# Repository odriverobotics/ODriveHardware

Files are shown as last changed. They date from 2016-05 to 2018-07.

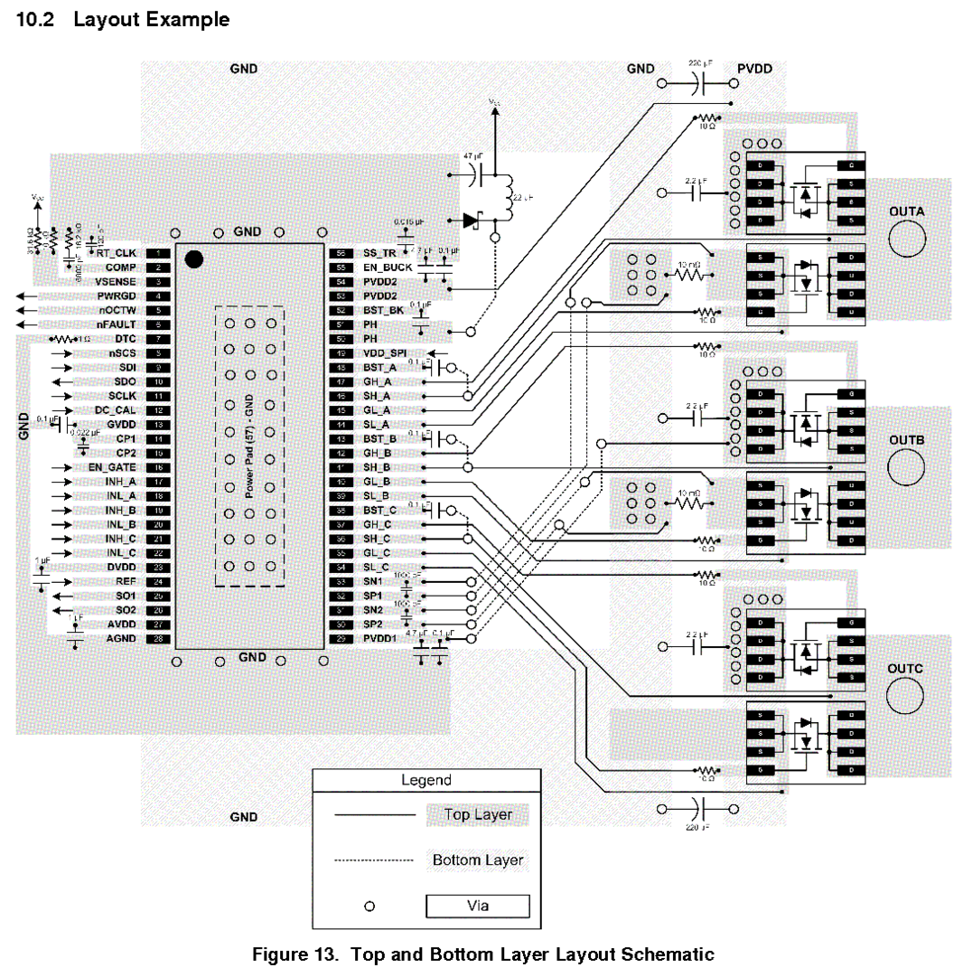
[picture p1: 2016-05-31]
v3/layoutexample.PNG

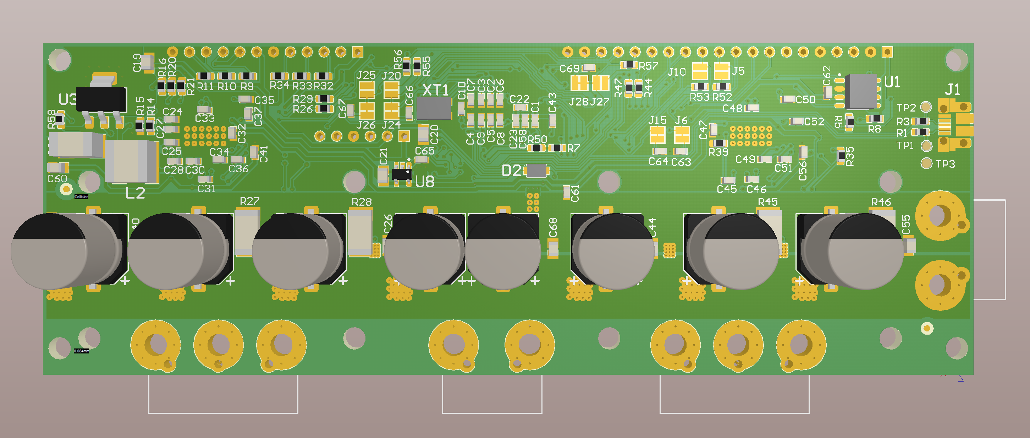
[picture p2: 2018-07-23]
v3/v3.5docs/v3.5_bottom.PNG

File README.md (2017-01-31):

# ODriveHardware
This project is all about accuratly driving brushless motors, for cheap. The aim is to make it possible to use inexpensive brushless motors in high performance robotics projects.
Like this (click for video):
Servo motor control demo (https://www.youtube.com/watch?v=WT4E5nb3KtY)

If you want to get your hands on a board, check out [this post](https://hackaday.io/project/11583-odrive-high-performance-motor-control/log/40702-boards-and-development).

This repository contains the circuit board design of ODrive. The other related repositories are:
* [ODriveFirmware](https://github.com/madcowswe/ODriveFirmware): Firmware that runs on the board.
* [ODrive](https://github.com/madcowswe/ODrive): Configuration and analysis scripts that runs on a PC.

There is also [ODriveFPGA](https://github.com/madcowswe/ODriveFPGA), which contains the FPGA logic and software that runs on the FPGA based ODrive. This is not currently in development, but may be resumed at some later date.

## Odrive v3 board
The pinout from the microcontroller to the board is documented [here](https://docs.google.com/spreadsheets/d/1QXDCs1IRtUyG__M_9WruWOheywb-GhOwFtfPcHuN2Fg/edit?usp=sharing).

### Pictures!
Odrive v3.1 top
Odrive v3.1 bottom

### ODrive v3.1 errata
* The silkscreen labels for the encoders (M0, M1) are reversed.
* The output impedence of the current amplifiers were not considered when designing the post-amplifier filters. Hence the response is about 5x slower than designed. Max allowed modulation index is therefore about 50%.

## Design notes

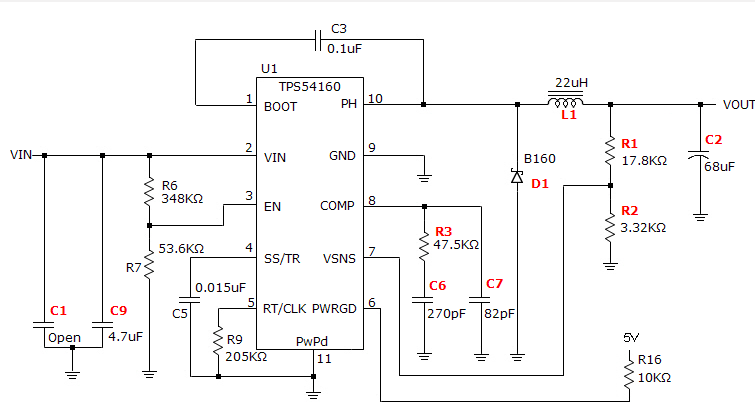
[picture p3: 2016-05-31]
v3/swticher pro design.PNG

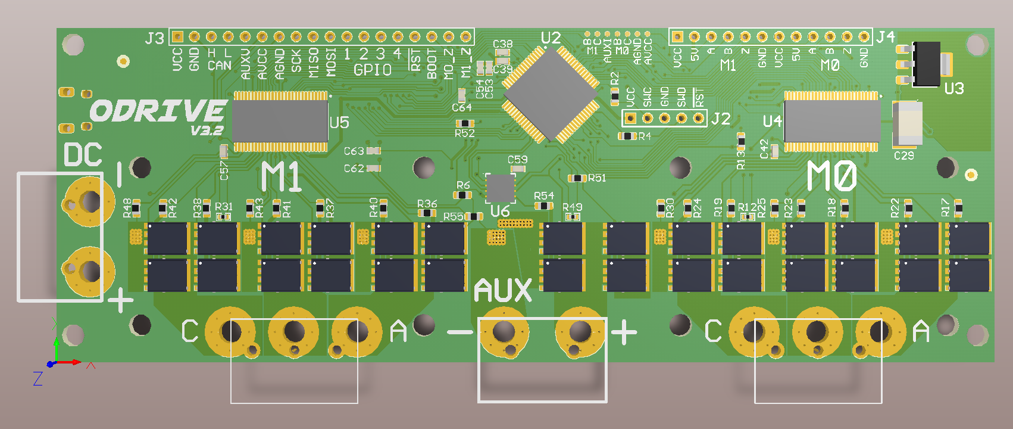
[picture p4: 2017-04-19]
v3/v3.2docs/v3.2_top.PNG

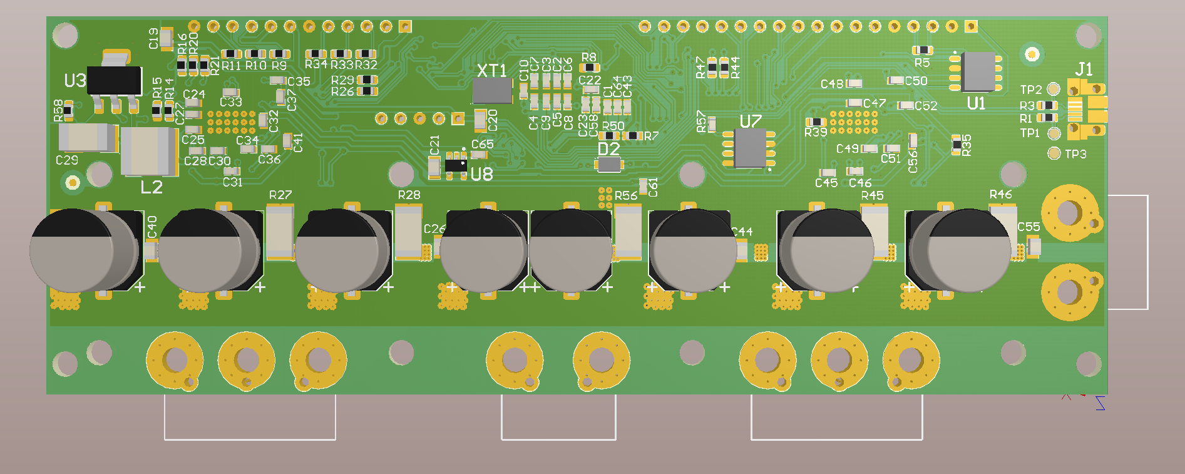
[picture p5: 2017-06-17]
v3/v3.3docs/v3.3_bottom.PNG

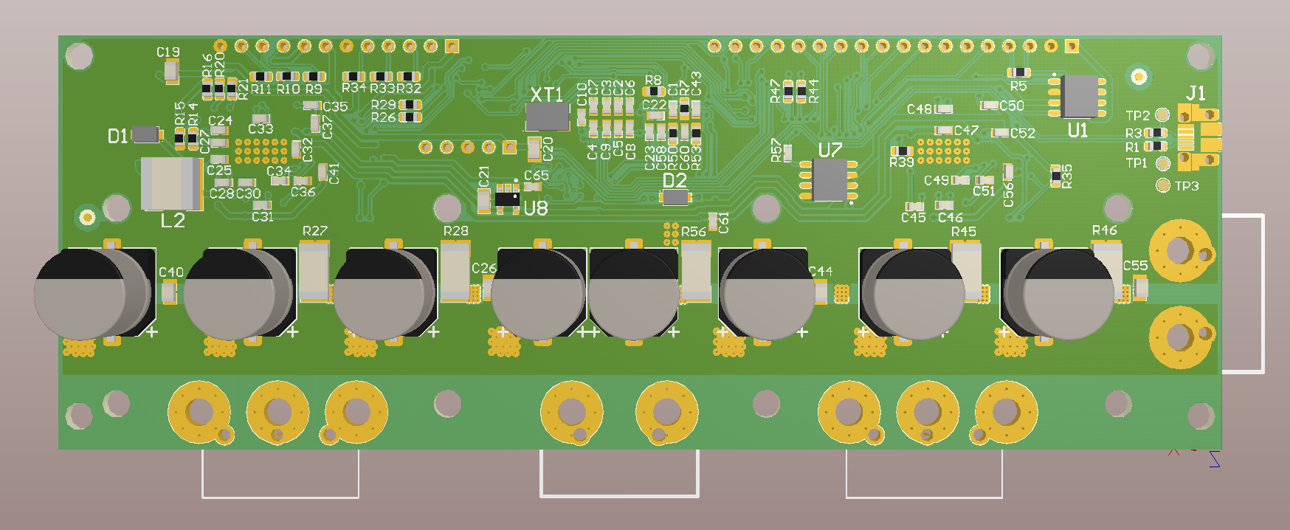
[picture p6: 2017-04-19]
v3/v3.2docs/v3.2_bottom.PNG

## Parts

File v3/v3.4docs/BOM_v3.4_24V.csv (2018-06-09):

Quantity | Designator | Description | Voltage - Rated | Comment | LibRef
14 | C1, C4, C5, C23, C32, C35, C37, C43, C47, C50, C52, C58, C61, C65 | CAP CER 2.2UF 16V X5R 0603 | 16V | 2.2µF | GRM188R61C225KE15D
2 | C2, C3 | CAP CER 10PF 50V NP0 0603 | 50V | 10pF | GRM1885C1H100JA01D
18 | C6, C7, C8, C9, C10, C22, C25, C28, C30, C31, C34, C41, C45, C46, C49, C56, C59, C63 | CAP CER 0.1UF 50V X7R 0603 | 50V | 0.1uF | GRM188R71H104KA93D
8 | C11, C12, C13, C14, C15, C16, C17, C18 | CAP, FP Series, 470 µF, 25 V, Radial Can - SMD, 10 mm |  | 470uF | EEEFP1E471AP
8 | C19, C20, C21, C26, C40, C44, C55, C60 | CAP CER 4.7UF 35V X5R 0805 | 35V | 4.7uF | GRM219R6YA475KA73D
1 | C24 | CAP CER 82PF 100V NP0 0603 | 100V | 82pF | GRM1885C2A820JA01D
1 | C27 | CAP CER 270PF 50V NP0 0603 | 50V | 270pF | GRM1885C1H271JA01D
1 | C29 | CAP TANT 68UF 16V 20% 2312 250mOhm |  | 68uF | T495C686M016ATE250
2 | C33, C48 | CAP CER 0.022UF 50V X7R 0603 | 50V | 0.022µF | GRM188R71H223KA01D
10 | C36, C38, C39, C42, C51, C53, C54, C57, C62, C64 | CAP CER 2200PF 50V NP0 0603 | 50V | 2200pF | GRM1885C1H222JA01D
2 | D1, D2 | Rectifier Diode, Single, 40 V, 1 A, SOD-123FL, 2, 550 mV |  |  | MBR140SFT1G
4 | FID1, FID2, FID3, FID4 | 1mm Fiducial with 2mm soldermask, 3mm keepout |  | FIDUCIAL | FIDUCIAL
12 | H1, H2, H3, H4, H5, H6, H7, H8, H9, H10, H11, H12 | M3 Hole with no copper |  |  | M3 Hole
1 | J1 | MICRO USB B, RECEPTACLE, SMT, RA, 5WAY |  |  | 10103594-0001LF
1 | J2 | Header, 5-Pin |  |  | Header 5
1 | J3 | Header, 18-Pin |  | Leftheader | Header 18
1 | J4 | Header, 12-Pin |  | Rightheader | Header 12
10 | J7, J8, J11, J12, J13, J16, J17, J18, J21, J22 | M3 Spade Terminal |  |  | M3 Spade Terminal
2 | J9, J23 | CONN TERM BLOCK 2POS 7.62MM |  | 1868076 | 1868076
2 | J14, J19 | CONN TERM BLOCK 3POS 7.62MM |  | 1704936 | 1704936
1 | L2 | INDUCTOR 22UH 1.4A 175.5 MOHM |  | 22uH | NR6028T220M
1 | LED1 | LED GREEN CLEAR 0603 SMD |  | Green | LTST-C190KGKT
28 | Q1, Q2, Q3, Q4, Q5, Q6, Q7, Q8, Q9, Q10, Q11, Q12, Q13, Q14, Q15, Q16, Q17, Q18, Q19, Q20, Q21, Q22, Q23, Q24, Q25, Q26, Q27, Q28 | MOSFET N-CH 30V 13A SO8FL |  | [NoValue], FILL_FOOTPRINT, [NoValue], FILL_FOOTPRINT, [NoValue], FILL_FOOTPRINT, [NoValue], [NoValue], [NoValue], [NoValue], [NoValue], [NoValue], [NoValue], FILL_FOOTPRINT, [NoValue], FILL_FOOTPRINT, [NoValue], FILL_FOOTPRINT, [NoValue], [NoValue], [NoValue], [NoValue], [NoValue], [NoValue], FILL_FOOTPRINT, [NoValue], [NoValue], [NoValue] | NTMFS4935NT1G
8 | R1, R2, R3, R4, R26, R29, R44, R47 | RES SMD 22 OHM 1% 1/10W 0603 |  | 22R | RC0603FR-0722RL
7 | R5, R25, R30, R43, R48, R55, R57 | RES SMD 120 OHM 1% 1/10W 0603 |  | 120R | RC0603FR-07120RL
1 | R6 | RES SMD 10K OHM 1% 1/10W 0603 |  | 10K | RC0603FR-0710KL
2 | R7, R58 | RES SMD 1K OHM 1% 1/10W 0603 |  | 1k | RC0603FR-071KL
2 | R8, R14 | RES SMD 47K OHM 1% 1/10W 0603 |  | 47K | RC0603FR-0747KL
10 | R9, R10, R11, R13, R20, R32, R33, R34, R35, R50 | RES SMD 3.3K OHM 1% 1/10W 0603 |  | 3.3k | RC0603FR-073K3L
3 | R12, R31, R49 | THERMISTOR 10K OHM NTC 0402 SMD |  | 10k | NCP15XH103F03RC
1 | R15 | RES SMD 220K OHM 1% 1/10W 0603 |  | 220k | RC0603FR-07220KL
3 | R16, R21, R39 | RES SMD 18K OHM 1% 1/10W 0603 |  | 18k | RC0603FR-0718KL
14 | R17, R18, R19, R22, R23, R24, R36, R37, R38, R40, R41, R42, R51, R54 | RES SMD 2.2 OHM 1% 1/10W 0603 |  | 2.2R | RC0603FR-072R2L
5 | R27, R28, R45, R46, R56 | RES SMD 0.0005 OHM 1% 3W 2512 |  | 500uOhm | CSR2512C0R0005F
1 | U1 |  |  | SN65HVD232D | SN65HVD232D
1 | U2 | ARM Cortex-M4 32-bit MCU+FPU, 210 DMIPS, 1024 kB Flash, 192 kB Internal RAM, 51 I/Os, 64-pin LQFP, -40 to 85 degC, Tray |  |  | STM32F405RGT6
1 | U3 | IC REG LDO 3.3V 1A SOT223 |  | 3.3V | AZ1117EH-3.3TRG1
2 | U4, U5 | MOTOR DRIVER, 3PH, 56HTSSOP |  |  | DRV8301
1 | U6 | DRIVER, MOSFET, HALF BRIDGE, WSON-8, 1A |  |  | LM5109BSD/NOPB
1 | U7 | ANALOG DEVICES Current Sense Amplifier, Bidirectional, 1, 130 µA, NSOIC |  |  | AD8418WBRZ
1 | U8 | IC REG LDO 3.3V 0.25A SOT23-5 |  | 3.3V | LP5907MFX-3.3/NOPB
1 | XT1 | Crystal 8MHz ±10ppm 10pF 200 Ohm -10°C ~ 60°C Surface Mount 4-SMD, No Lead (DFN, LCC) |  | 8 MHz | ABM3B-8.000MHZ-10-1-U-T

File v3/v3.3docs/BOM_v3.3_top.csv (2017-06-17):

Quantity | Designator | Description | Comment | LibRef | Layer
7 | C38, C39, C42, C53, C54, C57, C62 | CAP CER 2200PF 50V NP0 0603 | 2200pF | GRM1885C1H222JA01D | Top
2 | C59, C63 | CAP CER 0.1UF 25V X7R 0603 | 0.10µF | GRM188R71E104KA01D | Top
1 | D1 | Rectifier Diode, Single, 40 V, 1 A, SOD-123FL, 2, 550 mV |  | MBR140SFT1G | Top
2 | FID1, FID3 | 1mm Fiducial with 2mm soldermask, 3mm keepout | FIDUCIAL | FIDUCIAL | Top
12 | H1, H2, H3, H4, H5, H6, H7, H8, H9, H10, H11, H12 | M3 Hole with no copper |  | M3 Hole | Top
1 | J2 | Header, 5-Pin |  | Header 5 | Top
1 | J3 | Header, 18-Pin | Leftheader | Header 18 | Top
1 | J4 | Header, 12-Pin | Rightheader | Header 12 | Top
10 | J7, J8, J11, J12, J13, J16, J17, J18, J21, J22 | M3 Spade Terminal |  | M3 Spade Terminal | Top
2 | J9, J23 | CONN TERM BLOCK 2POS 7.62MM | 1868076 | 1868076 | Top
2 | J14, J19 | CONN TERM BLOCK 3POS 7.62MM | 1704936 | 1704936 | Top
1 | LED1 | LED GREEN CLEAR 0603 SMD | Green | LTST-C190KGKT | Top
28 | Q1, Q2, Q3, Q4, Q5, Q6, Q7, Q8, Q9, Q10, Q11, Q12, Q13, Q14, Q15, Q16, Q17, Q18, Q19, Q20, Q21, Q22, Q23, Q24, Q25, Q26, Q27, Q28 | MOSFET N-CH 30V 13A SO8FL |  | NTMFS4935NT1G | Top
2 | R2, R4 | RES SMD 22 OHM 1% 1/10W 0603 | 22R | RC0603FR-0722RL | Top
1 | R6 | RES SMD 10K OHM 1% 1/10W 0603 | 10K | RC0603FR-0710KL | Top
3 | R12, R31, R49 | THERMISTOR 10K OHM NTC 0402 SMD | 10k | NCP15XH103F03RC | Top
1 | R13 | RES SMD 3.3K OHM 1% 1/10W 0603 | 3.3k | RC0603FR-073K3L | Top
14 | R17, R18, R19, R22, R23, R24, R36, R37, R38, R40, R41, R42, R51, R54 | RES SMD 2.2 OHM 1% 1/10W 0603 | 2.2R | RC0603FR-072R2L | Top
5 | R25, R30, R43, R48, R55 | RES SMD 120 OHM 1% 1/10W 0603 | 120R | RC0603FR-07120RL | Top
1 | U2 | ARM Cortex-M4 32-bit MCU+FPU, 210 DMIPS, 1024 kB Flash, 192 kB Internal RAM, 51 I/Os, 64-pin LQFP, -40 to 85 degC, Tray |  | STM32F405RGT6 | Top
2 | U4, U5 | MOTOR DRIVER, 3PH, 56HTSSOP |  | DRV8301 | Top
1 | U6 | DRIVER, MOSFET, HALF BRIDGE, WSON-8, 1A |  | LM5109BSD/NOPB | Top

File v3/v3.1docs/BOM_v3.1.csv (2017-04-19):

Quantity | Designator | Description | Comment | LibRef
14 | C1, C4, C5, C23, C32, C35, C37, C43, C47, C50, C52, C58, C60, C61 | CAP CER 2.2UF 16V X5R 0603 | 2.2µF | GRM188R61C225KE15D
2 | C2, C3 | CAP CER 10PF 50V NP0 0603 | 10pF | GRM1885C1H100JA01D
18 | C6, C7, C8, C9, C10, C22, C25, C28, C30, C31, C34, C41, C45, C46, C49, C56, C59, C63 | CAP CER 0.1UF 25V X7R 0603 | 0.10µF | GRM188R71E104KA01D
8 | C11, C12, C13, C14, C15, C16, C17, C18 | CAP, FP Series, 470 µF, 25 V, Radial Can - SMD, 10 mm | 470uF | EEEFP1E471AP
7 | C19, C20, C21, C26, C40, C44, C55 | CAP CER 4.7UF 35V X5R 0805 | 4.7uF | GRM219R6YA475KA73D
1 | C24 | CAP CER 82PF 100V NP0 0603 | 82pF | GRM1885C2A820JA01D
1 | C27 | CAP CER 270PF 50V NP0 0603 | 270pF | GRM1885C1H271JA01D
1 | C29 | CAP TANT 68UF 16V 20% 2312 250mOhm | 68uF | T495C686M016ATE250
11 | C33, C36, C38, C39, C42, C48, C51, C53, C54, C57, C62 | CAP CER 0.022UF 25V X7R 0603 | 0.022µF | GRM188R71E223KA01D
2 | D1, D2 | Rectifier Diode, Single, 40 V, 1 A, SOD-123FL, 2, 550 mV |  | MBR140SFT1G
12 | H1, H2, H3, H4, H5, H6, H7, H8, H9, H10, H11, H12 | M3 Hole with no copper |  | M3 Hole
1 | J1 | MICRO USB B, RECEPTACLE, SMT, RA, 5WAY |  | 10103594-0001LF
3 | J2, J10, J15 | Header, 5-Pin |  | Header 5
1 | J3 | Header, 3-Pin |  | Header 3
1 | J4 | Header, 4-Pin |  | Header 4
1 | J5 | Header, 3-Pin, Dual row |  | Header 3X2
1 | J6 | Header, 8-Pin |  | Header 8
10 | J7, J8, J11, J12, J13, J16, J17, J18, J21, J22 | M3 Spade Terminal |  | M3 Spade Terminal
2 | J9, J23 | MULTICOMP Wire-To-Board Terminal Block, 2, 600 V, 30 A, 24 AWG, 10 AWG |  | MC000054
2 | J14, J19 | TERMINAL BLOCK, WIRE TO BRD, 3POS, 10AWG |  | MC000051
1 | J20 | Socket | AuxV | Socket
1 | L1 | FERRITE BEAD, 0.1OHM, 2A, 0805 | 600ohm | 2508056017Y2
1 | L2 | INDUCTOR 22UH 1.4A 175.5 MOHM | 22uH | NR6028T220M
28 | Q1, Q2, Q3, Q4, Q5, Q6, Q7, Q8, Q9, Q10, Q11, Q12, Q13, Q14, Q15, Q16, Q17, Q18, Q19, Q20, Q21, Q22, Q23, Q24, Q25, Q26, Q27, Q28 | MOSFET, N CH, 30V, 70A, SO-8 FL |  | NTMFS4937NT1G
13 | R1, R2, R3, R4, R25, R26, R29, R30, R43, R44, R47, R48, R55 | RES SMD 22 OHM 1% 1/10W 0603 | 22R | RC0603FR-0722RL
1 | R5 | RES SMD 120 OHM 1% 1/10W 0603 | 120R | RC0603FR-07120RL
2 | R6, R52 | RES SMD 10K OHM 1% 1/10W 0603 | 10K | RC0603FR-0710KL
8 | R7, R9, R10, R11, R32, R33, R34, R53 | RES SMD 1K OHM 1% 1/10W 0603 | 1k | RC0603FR-071KL
2 | R8, R14 | RES SMD 47K OHM 1% 1/10W 0603 | 47K | RC0603FR-0747KL
3 | R12, R31, R49 | THERMISTOR 10K OHM NTC 0402 SMD | 10k | NCP15XH103F03RC
4 | R13, R20, R35, R50 | RES SMD 3.3K OHM 1% 1/10W 0603 | 3.3k | RC0603FR-073K3L
1 | R15 | RES SMD 220K OHM 1% 1/10W 0603 | 220k | RC0603FR-07220KL
3 | R16, R21, R39 | RES SMD 18K OHM 1% 1/10W 0603 | 18k | RC0603FR-0718KL
14 | R17, R18, R19, R22, R23, R24, R36, R37, R38, R40, R41, R42, R51, R54 | RES SMD 2.2 OHM 1% 1/10W 0603 | 2.2R | RC0603FR-072R2L
5 | R27, R28, R45, R46, R56 | RES SMD 0.0005 OHM 1% 3W 2512 | 500uOhm | CSR2512C0R0005F
1 | U1 | 3.3-V CAN Bus Transceiver |  | SN65HVD232D
1 | U2 | ARM Cortex-M4 32-bit MCU+FPU, 210 DMIPS, 1024 kB Flash, 192 kB Internal RAM, 51 I/Os, 64-pin LQFP, -40 to 85 degC, Tray |  | STM32F405RGT6
1 | U3 | IC, LDO, REG, 3.3V, SOT223 | 3.3V | AP1117E33G-13
2 | U4, U5 | MOTOR DRIVER, 3PH, 56HTSSOP |  | DRV8301
1 | U6 | DRIVER, MOSFET, HALF BRIDGE, WSON-8, 1A |  | LM5109BSD/NOPB
1 | U7 | ANALOG DEVICES Current Sense Amplifier, Bidirectional, 1, 130 µA, NSOIC |  | AD8418WBRZ
1 | XT1 | Crystal 8MHz ±10ppm 10pF 200 Ohm -10°C ~ 60°C Surface Mount 4-SMD, No Lead (DFN, LCC) | 8 MHz | ABM3B-8.000MHZ-10-1-U-T

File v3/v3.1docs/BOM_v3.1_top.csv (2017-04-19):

Quantity | Designator | Description | Comment | LibRef | Layer
1 | C29 | CAP TANT 68UF 16V 20% 2312 250mOhm | 68uF | T495C686M016ATE250 | Top
7 | C38, C39, C42, C53, C54, C57, C62 | CAP CER 0.022UF 25V X7R 0603 | 0.022µF | GRM188R71E223KA01D | Top
2 | C59, C63 | CAP CER 0.1UF 25V X7R 0603 | 0.10µF | GRM188R71E104KA01D | Top
12 | H1, H2, H3, H4, H5, H6, H7, H8, H9, H10, H11, H12 | M3 Hole with no copper |  | M3 Hole | Top
3 | J2, J10, J15 | Header, 5-Pin |  | Header 5 | Top
1 | J3 | Header, 3-Pin |  | Header 3 | Top
1 | J4 | Header, 4-Pin |  | Header 4 | Top
1 | J5 | Header, 3-Pin, Dual row |  | Header 3X2 | Top
1 | J6 | Header, 8-Pin |  | Header 8 | Top
10 | J7, J8, J11, J12, J13, J16, J17, J18, J21, J22 | M3 Spade Terminal |  | M3 Spade Terminal | Top
2 | J9, J23 | MULTICOMP Wire-To-Board Terminal Block, 2, 600 V, 30 A, 24 AWG, 10 AWG |  | MC000054 | Top
2 | J14, J19 | TERMINAL BLOCK, WIRE TO BRD, 3POS, 10AWG |  | MC000051 | Top
1 | J20 | Socket | AuxV | Socket | Top
28 | Q1, Q2, Q3, Q4, Q5, Q6, Q7, Q8, Q9, Q10, Q11, Q12, Q13, Q14, Q15, Q16, Q17, Q18, Q19, Q20, Q21, Q22, Q23, Q24, Q25, Q26, Q27, Q28 | MOSFET, N CH, 30V, 70A, SO-8 FL |  | NTMFS4937NT1G | Top
7 | R2, R4, R25, R30, R43, R48, R55 | RES SMD 22 OHM 1% 1/10W 0603 | 22R | RC0603FR-0722RL | Top
1 | R5 | RES SMD 120 OHM 1% 1/10W 0603 | 120R | RC0603FR-07120RL | Top
2 | R6, R52 | RES SMD 10K OHM 1% 1/10W 0603 | 10K | RC0603FR-0710KL | Top
3 | R12, R31, R49 | THERMISTOR 10K OHM NTC 0402 SMD | 10k | NCP15XH103F03RC | Top
1 | R13 | RES SMD 3.3K OHM 1% 1/10W 0603 | 3.3k | RC0603FR-073K3L | Top
14 | R17, R18, R19, R22, R23, R24, R36, R37, R38, R40, R41, R42, R51, R54 | RES SMD 2.2 OHM 1% 1/10W 0603 | 2.2R | RC0603FR-072R2L | Top
1 | U1 | 3.3-V CAN Bus Transceiver |  | SN65HVD232D | Top
1 | U2 | ARM Cortex-M4 32-bit MCU+FPU, 210 DMIPS, 1024 kB Flash, 192 kB Internal RAM, 51 I/Os, 64-pin LQFP, -40 to 85 degC, Tray |  | STM32F405RGT6 | Top
1 | U3 | IC, LDO, REG, 3.3V, SOT223 | 3.3V | AP1117E33G-13 | Top
2 | U4, U5 | MOTOR DRIVER, 3PH, 56HTSSOP |  | DRV8301 | Top
1 | U6 | DRIVER, MOSFET, HALF BRIDGE, WSON-8, 1A |  | LM5109BSD/NOPB | Top

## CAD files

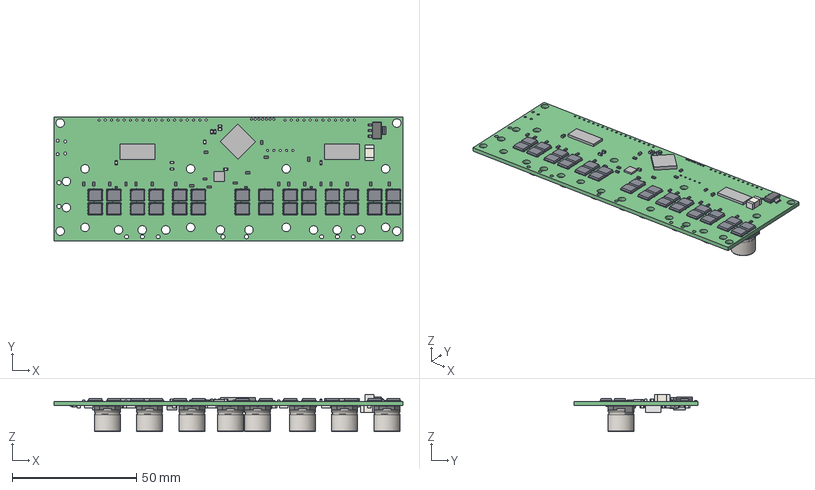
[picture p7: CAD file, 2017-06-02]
v3/v3.2docs/PCB_v3.2.step
140.5 x 50.0 x 15.0 mm
Board
SOT23-5
Extruded x 201
RES_0402_(1005_metric) x 3
RES_0603_(1608_metric) x 48
SOT223-4
User_Library-DFN5x6_SO8FL_Extruded x 56
User_Library-DFN5x6_SO8FL_Extruded_2 x 56
User_Library-DFN5x6_SO8FL_Cylinder x 28
User_Library-DFN5x6_SO8FL_Extruded_3 x 28
User_Library-DFN5x6_SO8FL_Extruded_4 x 28
User_Library-DFN5x6_SO8FL_Extruded_5 x 112
User_Library-DFN5x6_SO8FL_Extruded_6 x 28
CAP_Alum_Elec_Size_G x 8

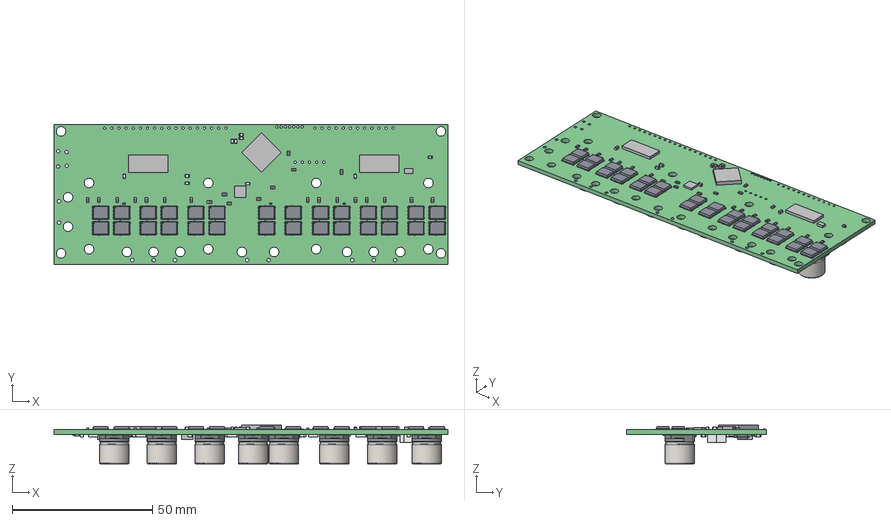
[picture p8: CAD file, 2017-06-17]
v3/v3.3docs/PCB_v3.3.step
140.5 x 50.0 x 13.8 mm
Board
Extruded x 198
SOT23-5
RES_0402_(1005_metric) x 3
RES_0603_(1608_metric) x 47
SOT223-4
User_Library-DFN5x6_SO8FL_Extruded x 56
User_Library-DFN5x6_SO8FL_Extruded_2 x 56
User_Library-DFN5x6_SO8FL_Cylinder x 28
User_Library-DFN5x6_SO8FL_Extruded_3 x 28
User_Library-DFN5x6_SO8FL_Extruded_4 x 28
User_Library-DFN5x6_SO8FL_Extruded_5 x 112
User_Library-DFN5x6_SO8FL_Extruded_6 x 28
CAP_Alum_Elec_Size_G x 8
LED_0603_APT1608_GREEN

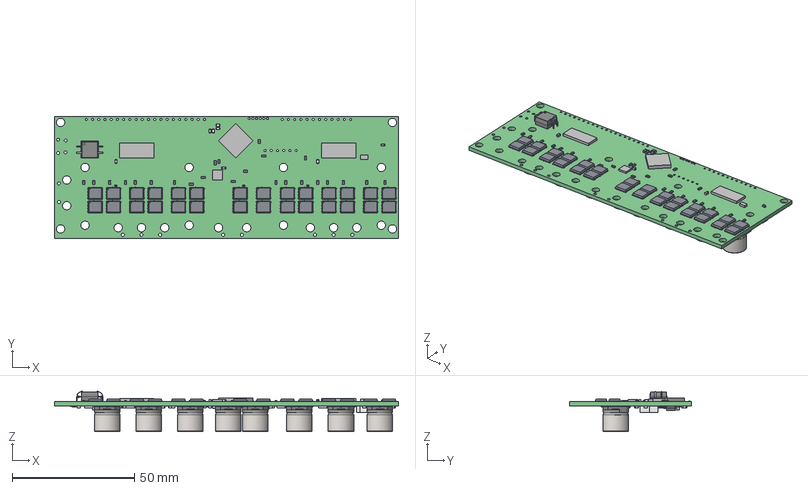
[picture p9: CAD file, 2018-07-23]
v3/v3.5docs/PCB_v3.5.step
140.5 x 50.0 x 16.4 mm
Board
RES_0603_(1608_metric) x 53
Extruded x 206
Open_CASCADE_STEP_translator_6.8_2.1
Open_CASCADE_STEP_translator_6.8_2.2.1
Leader x 4
SOT23-5
RES_0402_(1005_metric) x 3
SOT223-4
User_Library-DFN5x6_SO8FL_Extruded x 56
User_Library-DFN5x6_SO8FL_Extruded_2 x 56
User_Library-DFN5x6_SO8FL_Cylinder x 28
User_Library-DFN5x6_SO8FL_Extruded_3 x 28
User_Library-DFN5x6_SO8FL_Extruded_4 x 28
User_Library-DFN5x6_SO8FL_Extruded_5 x 112
User_Library-DFN5x6_SO8FL_Extruded_6 x 28
CAP_Alum_Elec_Size_G x 8
LED_0603_APT1608_GREEN

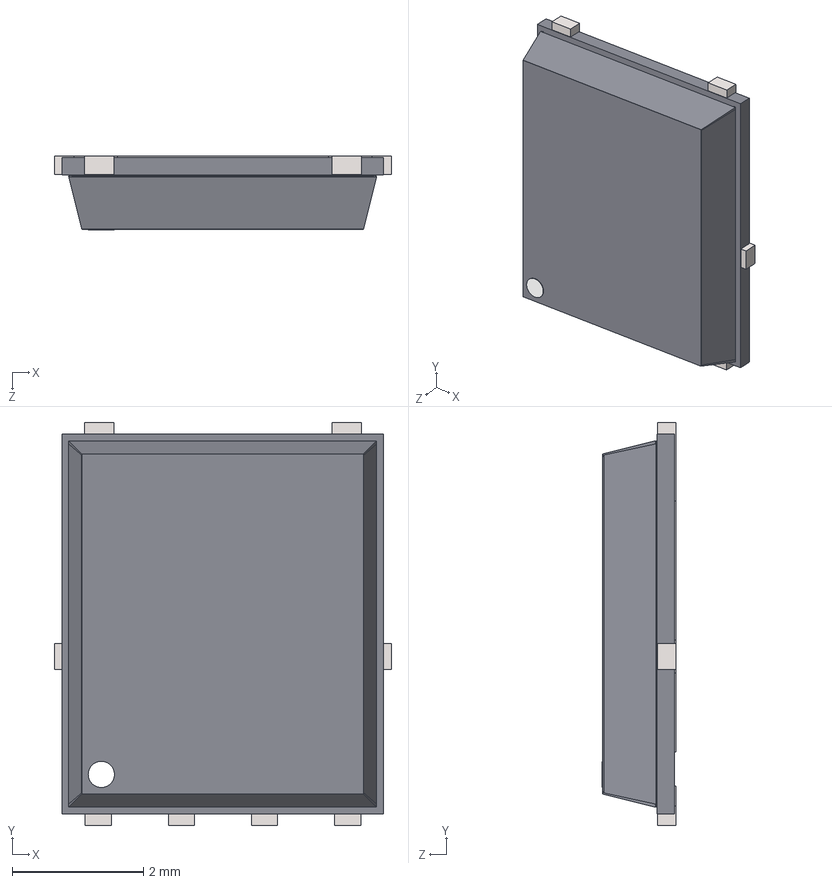
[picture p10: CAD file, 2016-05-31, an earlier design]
v2/User Library-DFN5x6_SO8FL.STEP
5.15 x 6.15 x 1.13 mm
User Library-DFN5x6_SO8FL_Extruded x 2
User Library-DFN5x6_SO8FL_Extruded_2 x 2
User Library-DFN5x6_SO8FL_Cylinder
User Library-DFN5x6_SO8FL_Extruded_3
User Library-DFN5x6_SO8FL_Extruded_4
User Library-DFN5x6_SO8FL_Extruded_5 x 4
User Library-DFN5x6_SO8FL_Extruded_6

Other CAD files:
v3/v3.4docs/PCB_v3.4.step

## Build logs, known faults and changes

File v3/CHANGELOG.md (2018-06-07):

## [3.5] - 2018-04-24
### Added
* Ground planes: 4 layer board
  * Logic side planes are GND, AGND
  * Power side planes are PGND, DC_BUS
* GPIO 6,7,8
  * Expose TIM2 CH 1,2
  * One extra ADC capable pin
  * See: https://docs.google.com/spreadsheets/d/1QXDCs1IRtUyG__M_9WruWOheywb-GhOwFtfPcHuN2Fg/edit#gid=949495736
* Two channel DIP switch:
  * Actuate BOOT0 pin to enter bootloader
  * Connect/disconnect CAN termination resistor
* Optional RC filters on step/dir/en and UART lines: GPIO 1,2,6,7,8.
* Strong pull-down resistors on the control signals to the AUX half-H to counteract weak pullups actiavated in DFU mode.
* Two GND pins on J3
* 5V pin on J2

### Changed
* Moved DVDD cap from AGND to GND
* Moved GPIO_5 to PC4
* Change C1 from 2.2uF to 270pF for cycle by cycle Vbus check
* ~~Board voltage determined by stickers (not silkscreen)~~

### Removed
* DC_CAL signals
* AUX current sense amplifier

### Fixed
* Clearance of shunt resistor kelvin connections now enforced with net-tie
* Silkscreen on J2 VCC -> 3.3V

## [3.4] - 2017-11-04
### Changed
* Fixed grounding issue: split digital and power grounds
* Fixed extra apparent shunt resistance, which caused a current measurement scale error
* Change VCC silkscreen to 3.3V

## [3.3] - 2017-06-17
### Added
* Power LED
* Pads on DC rail, for secondary power connection, on the opposite side of main power connector

### Changed
* GPIO Pinout. See: https://docs.google.com/spreadsheets/d/1QXDCs1IRtUyG__M_9WruWOheywb-GhOwFtfPcHuN2Fg/edit#gid=404444347
  * This enables the use of TIM5 on all GPIO pins, which is good for step/dir capture.
  * All GPIO pins are 5v tolerant.
  * 5th GPIO pin now available
* Fliped LDO and C29 to bot side, for better clearance on top side for enclosure style heatsinking.
* Changed all screw terminals to 7.62mm pitch
* Encoder pullup resistance 1k -> 3.3k, to be compatible with 2mA push-pull encoders without desoldering.

### Removed
* AUX_V voltage measurement no longer available.

## [3.2] - 2017-04-19
### Added
* Test-points for most interesting analogue signals
* Break out of the SPI port
* Precision LDO for AVCC (analog VCC)
* Fiducials

### Changed
* Fix current sensor filter capacitor values
* Consolidate all 0.1" headers into two long rows
* Change MOSFETs to a slightly better Rdson version (30% better)
* Adjust heatsink holes
* Improve labling

### Removed
* The confusing EV (Encoder Voltage) rail.

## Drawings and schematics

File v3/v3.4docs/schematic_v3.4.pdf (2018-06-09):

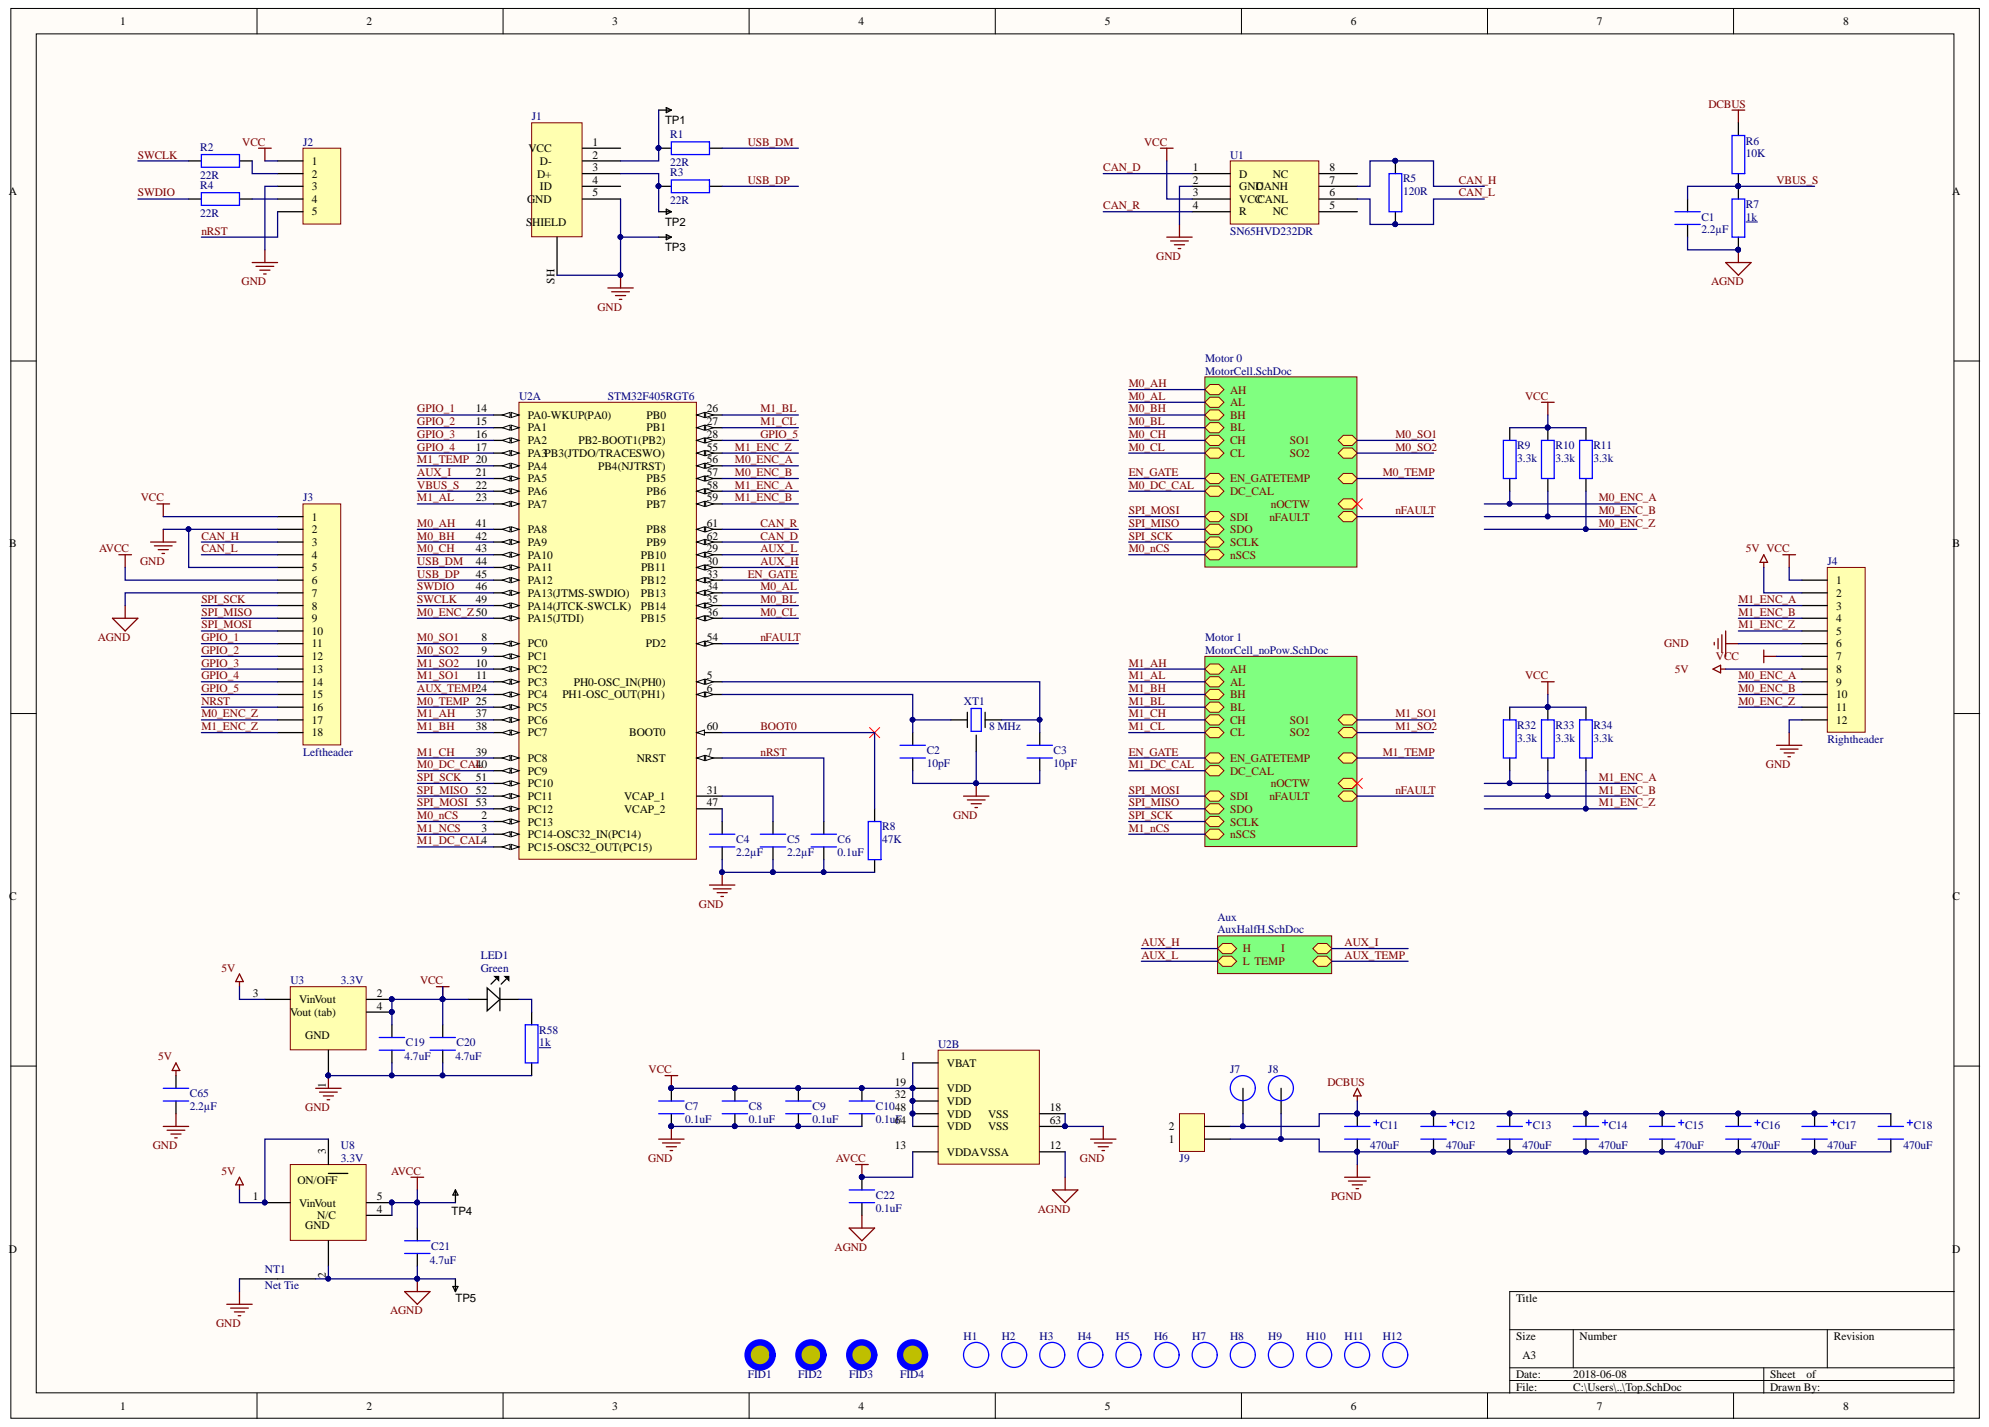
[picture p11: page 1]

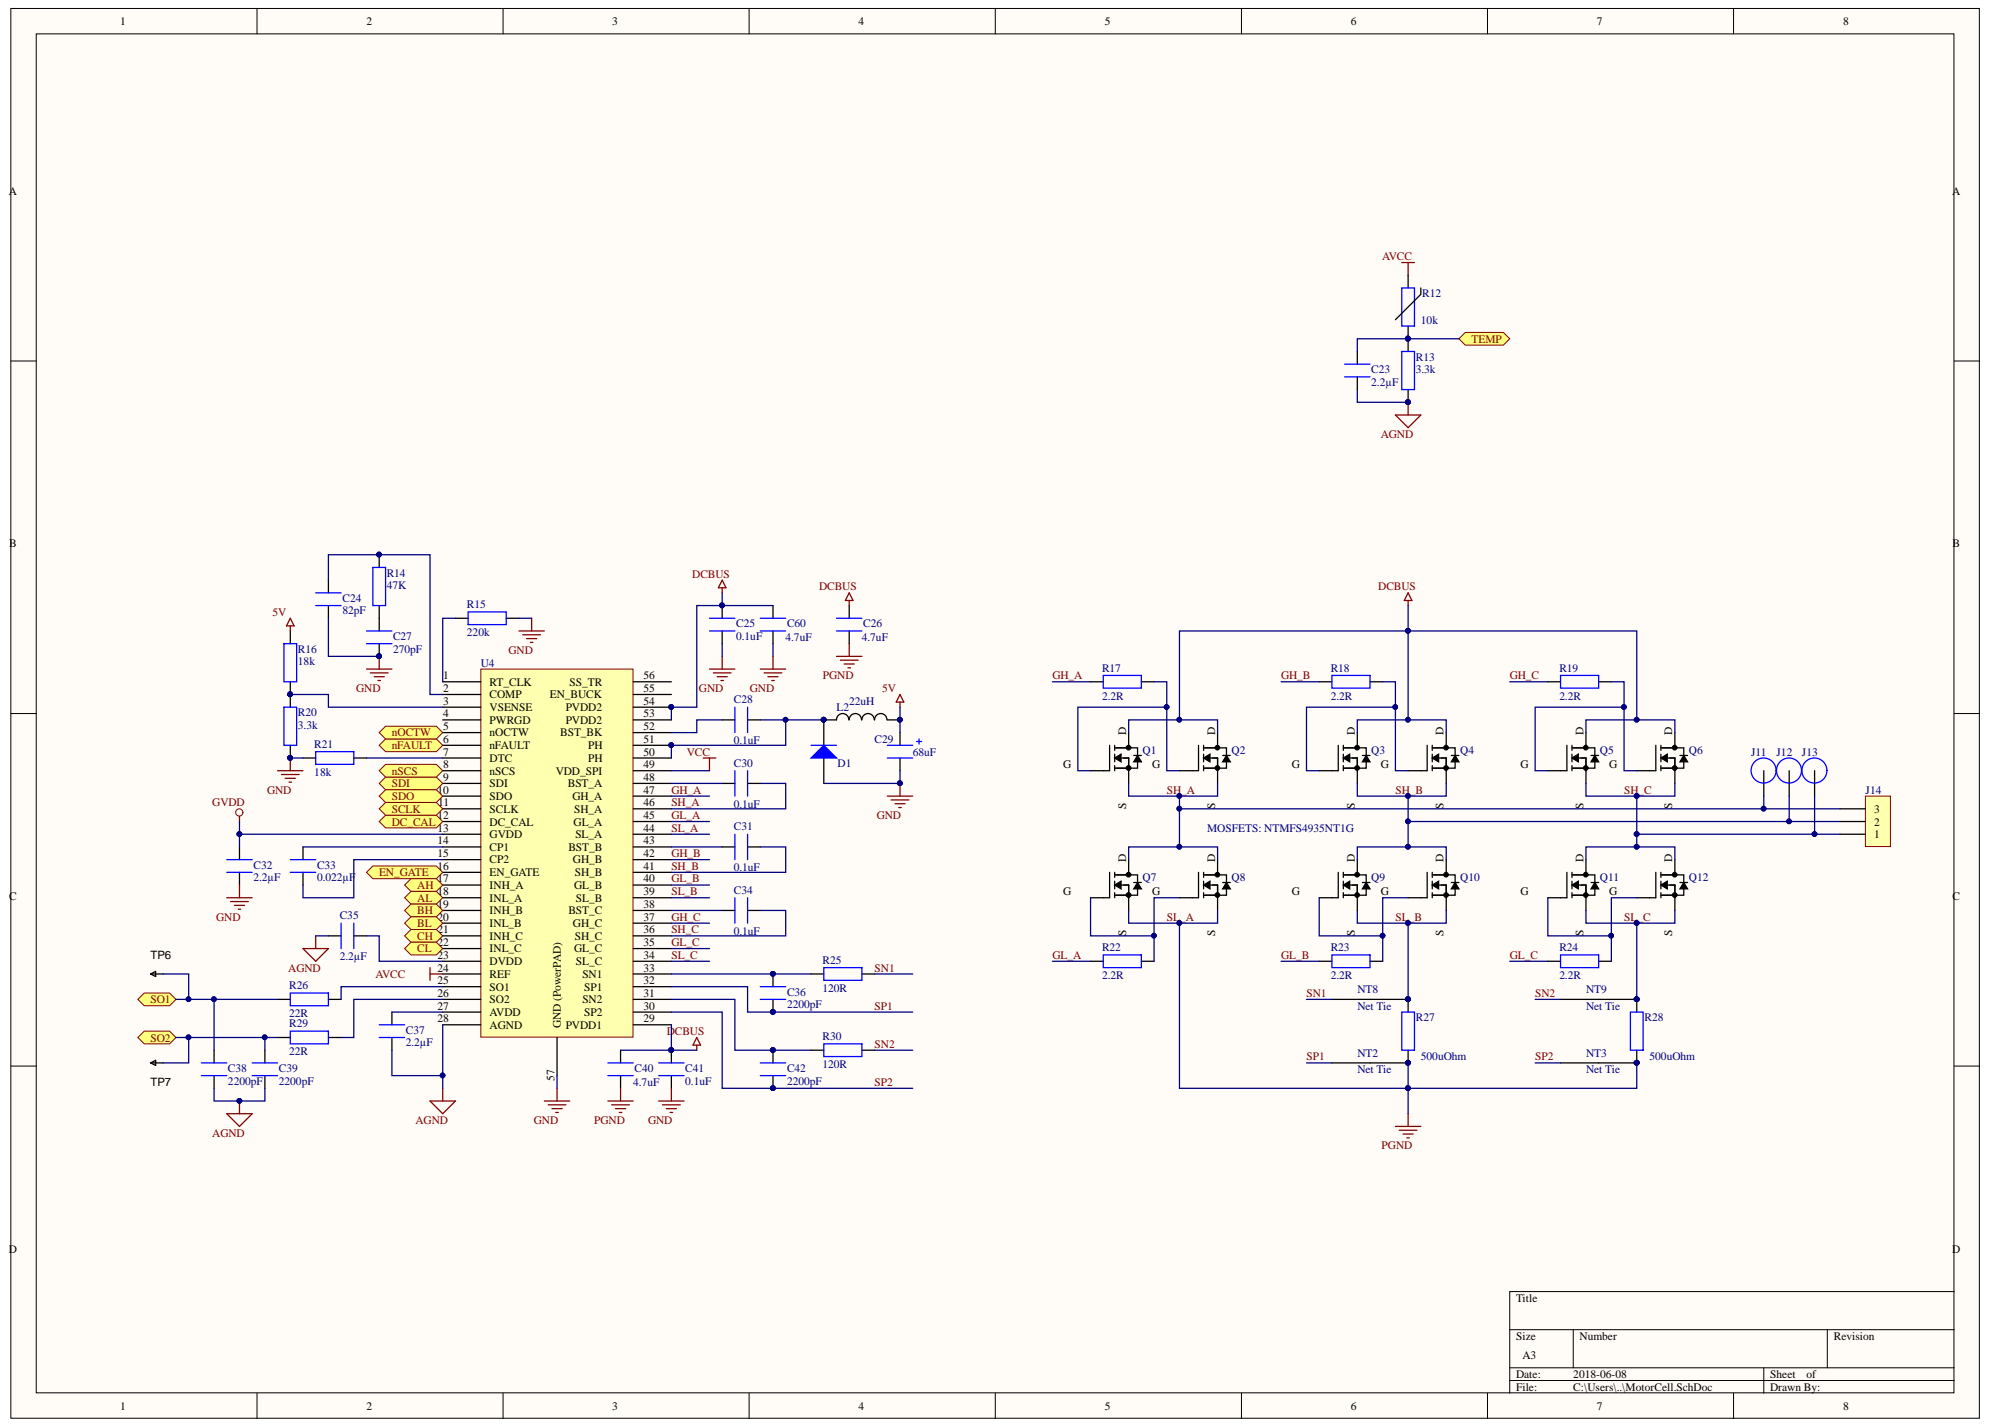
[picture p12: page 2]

R21 | PWRGD 4

nFAULT 6 | | VCC

CP1 14
CP2 15 | | GH_B | 0.1uF

C33 EN_GATE 0.022µF AH | EN_GATE 16 | | SH_B

INH_A 17 | GL_B
INL_A 18 | SL_B

C37 | | DCBUS | R30
2.2µF

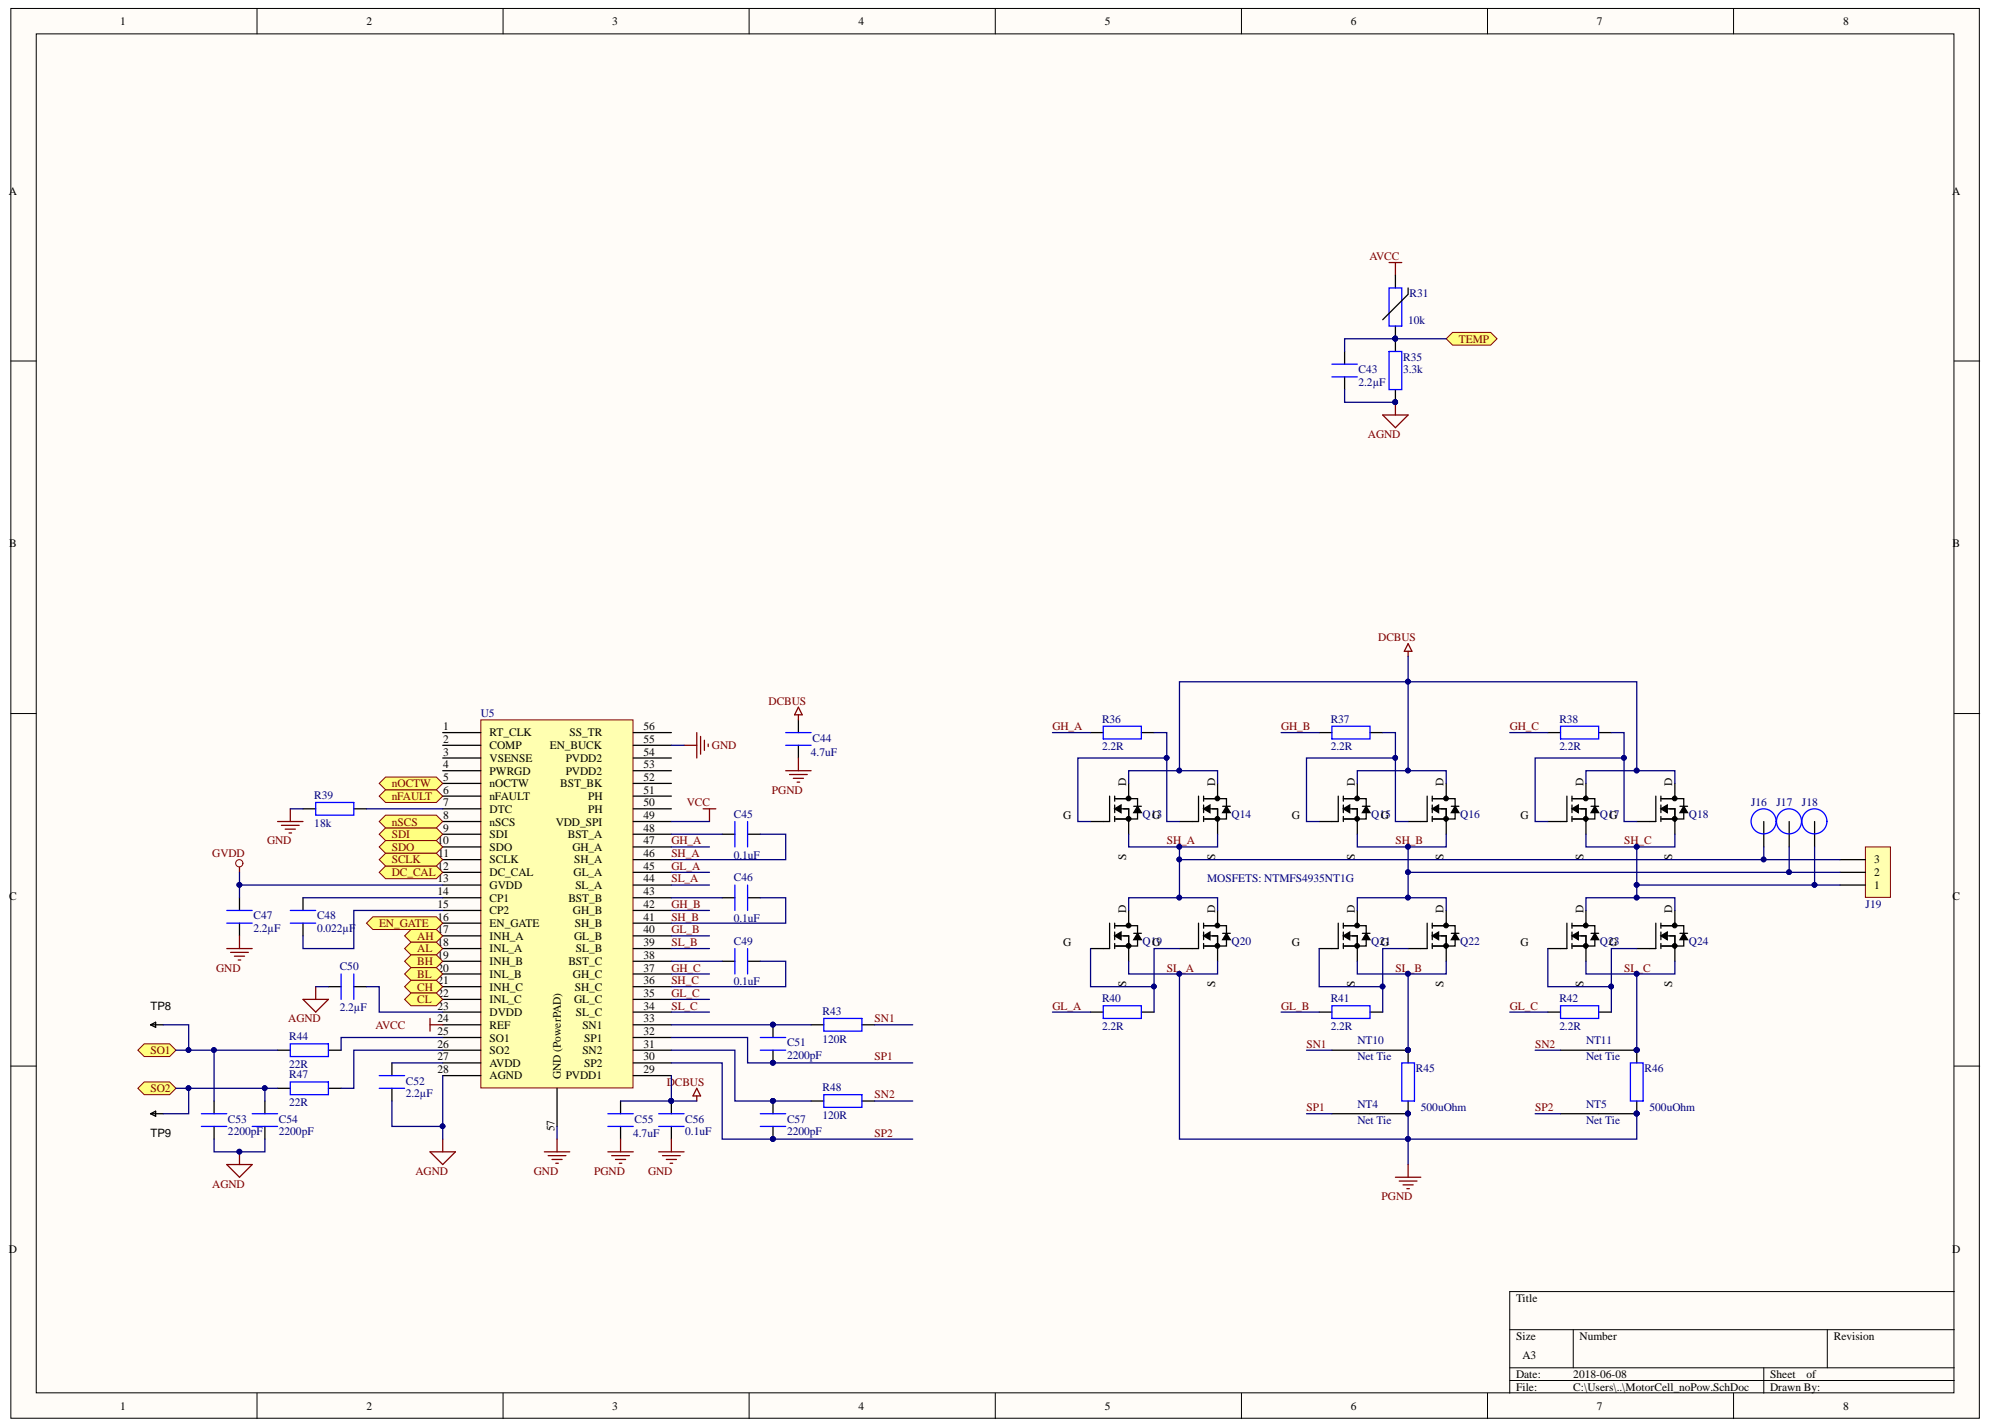
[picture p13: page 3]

GVDD 13 | SL_A
CP1 14
CP2 15 | | GH_B | 0.1uF

C48 EN_GATE 0.022µF AH | | EN_GATE 16 | | SH_B

INH_A 17 | GL_B
INL_A 18 | SL_B

SO2 26 | | C51
AVDD 27 | | 2200pF

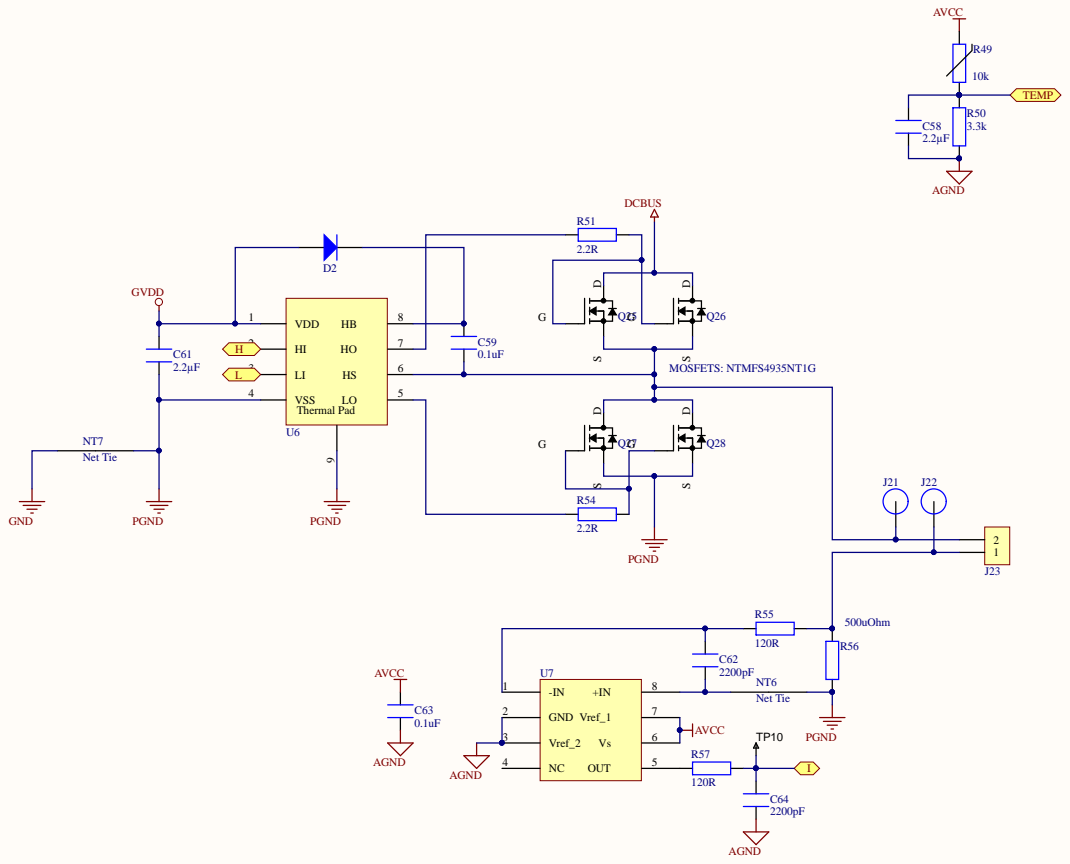
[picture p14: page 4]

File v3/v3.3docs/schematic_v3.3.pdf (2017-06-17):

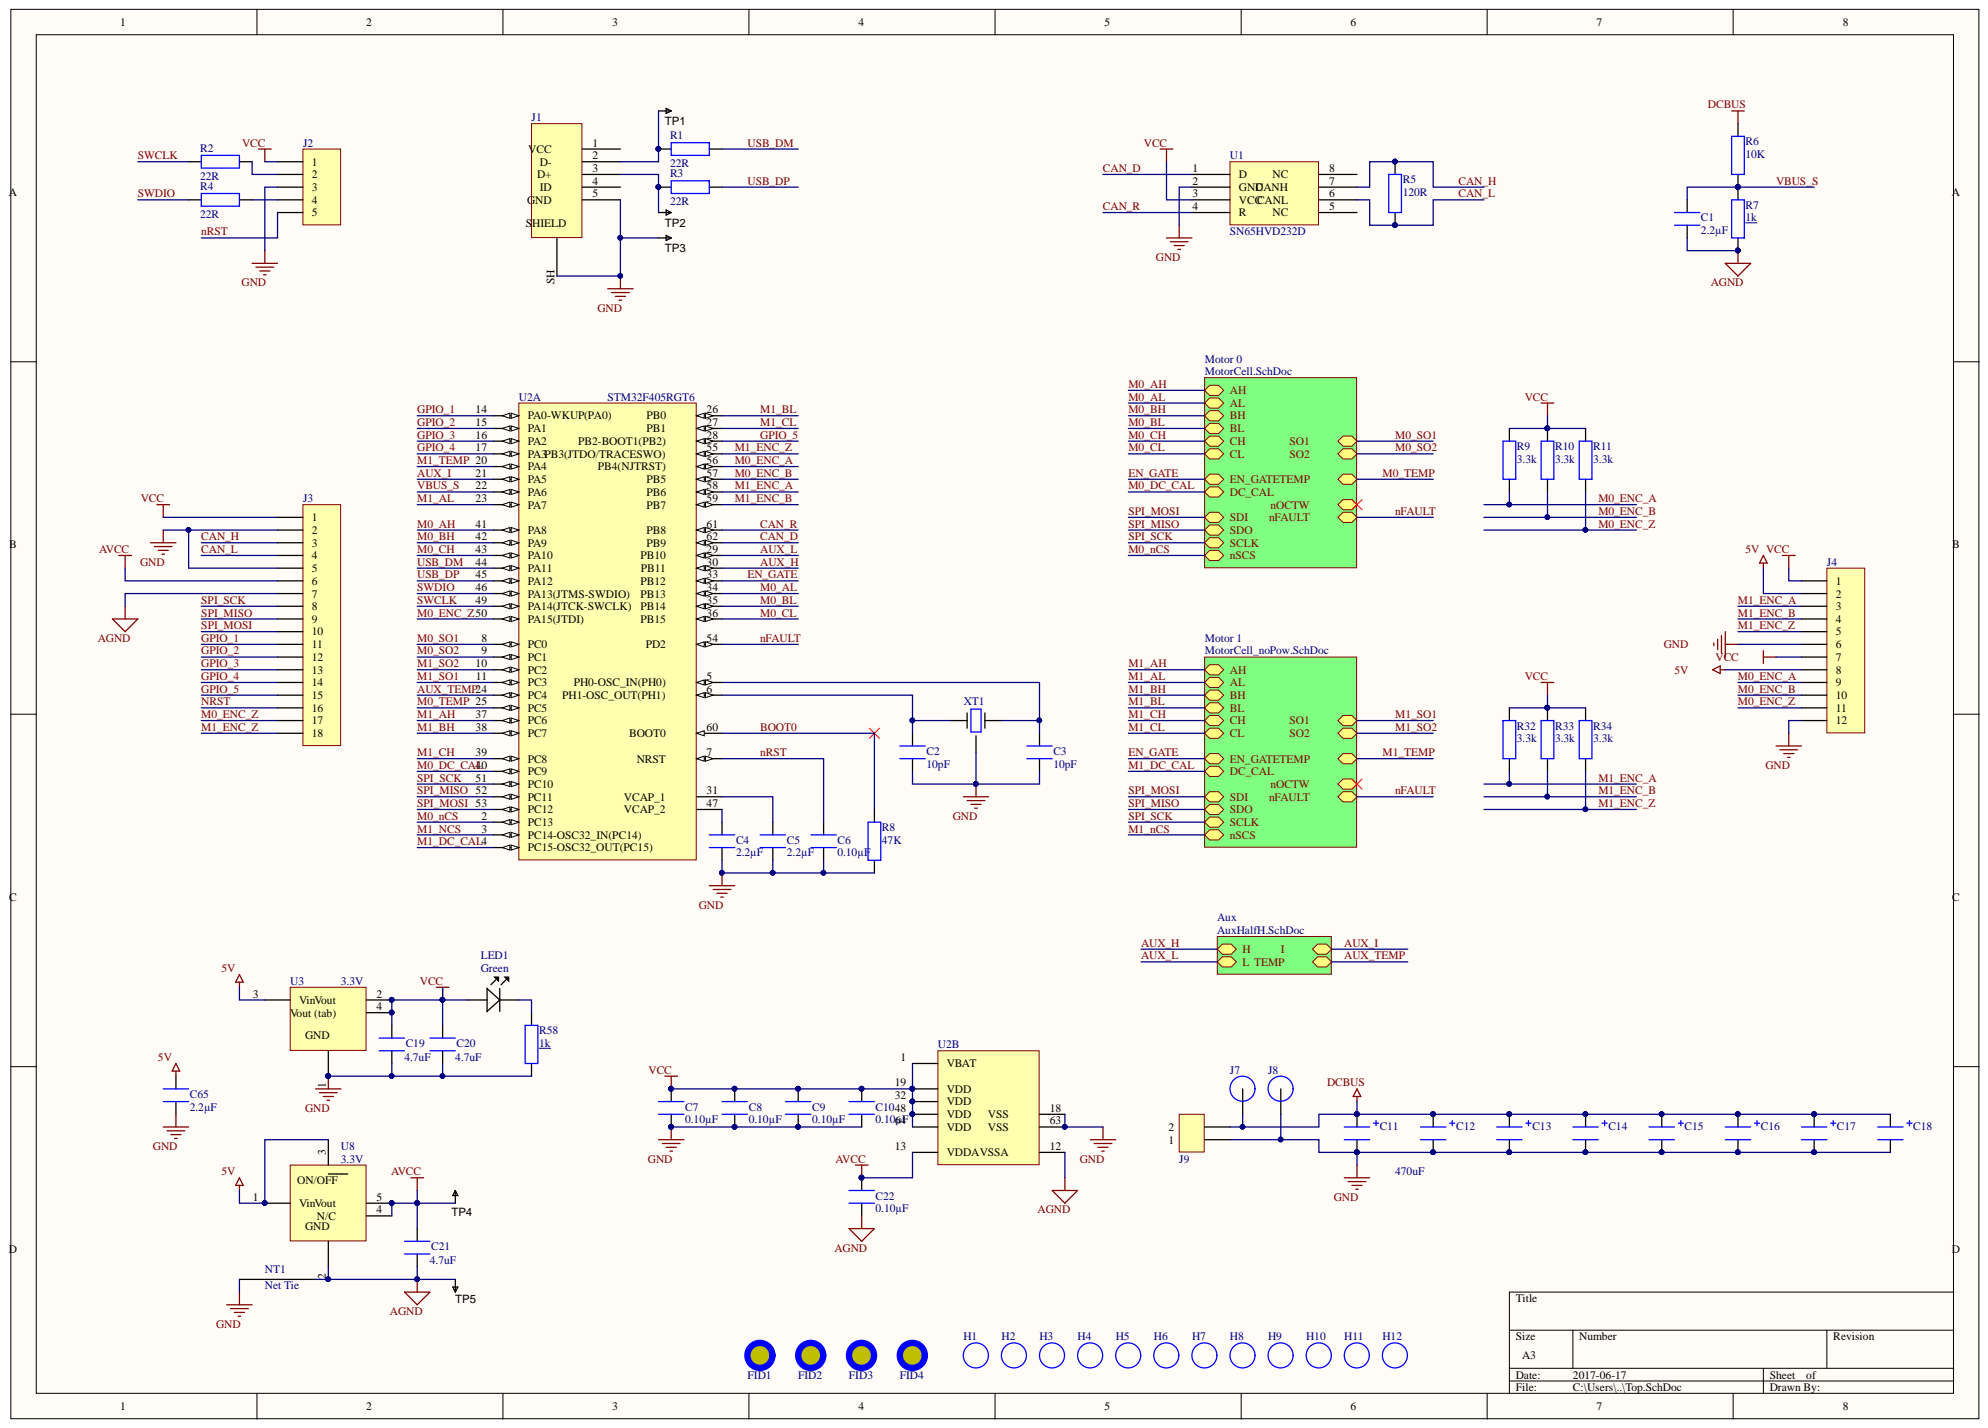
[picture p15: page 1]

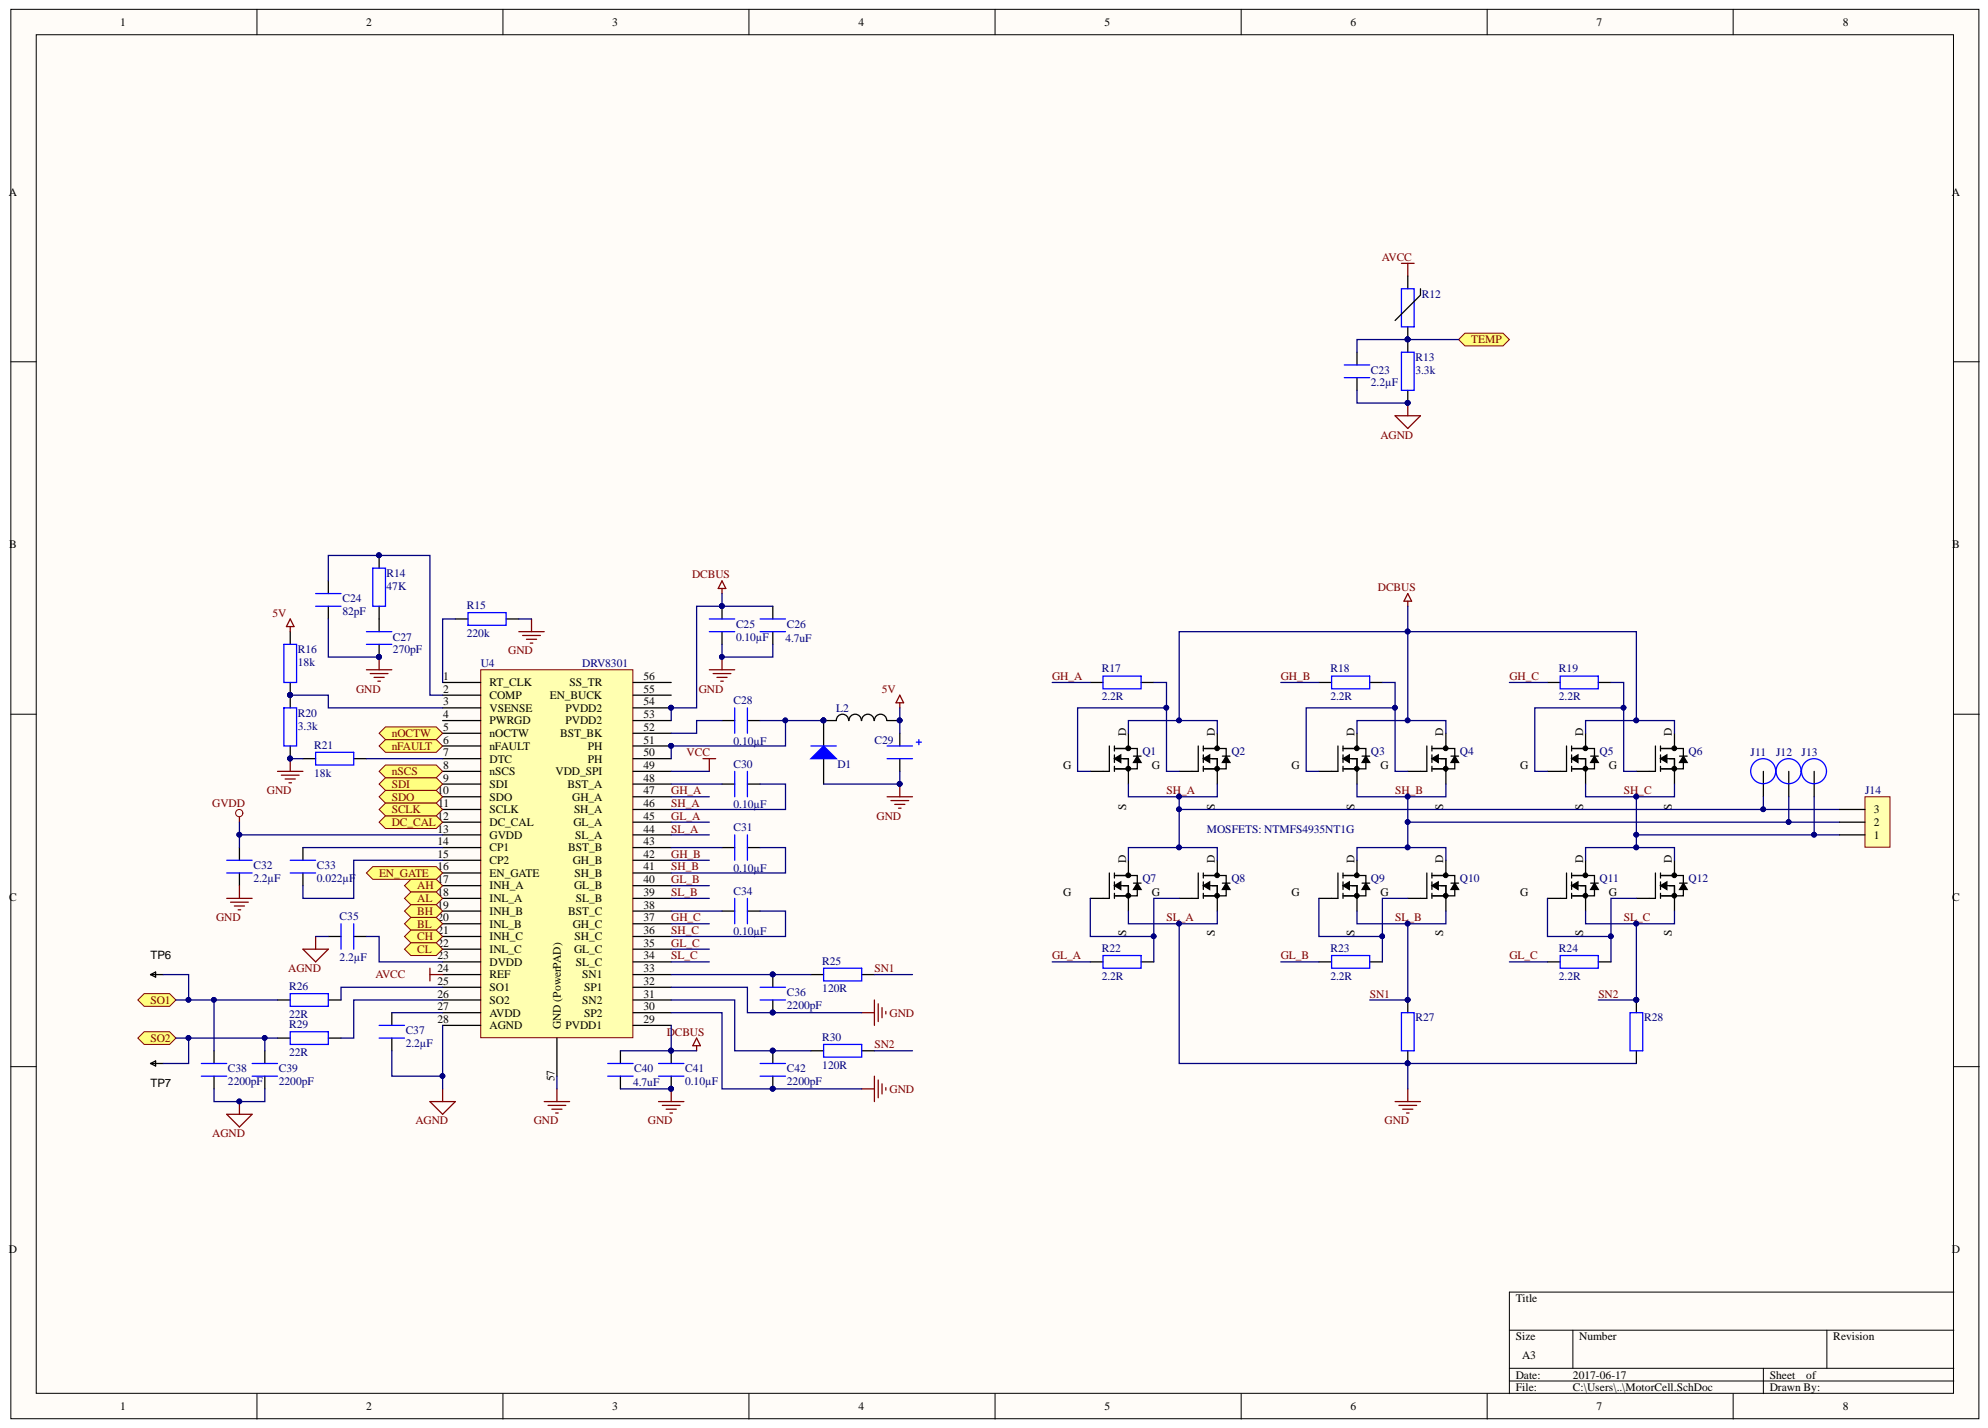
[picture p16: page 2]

C33 EN_G ATEAHAL 0.022 µ F

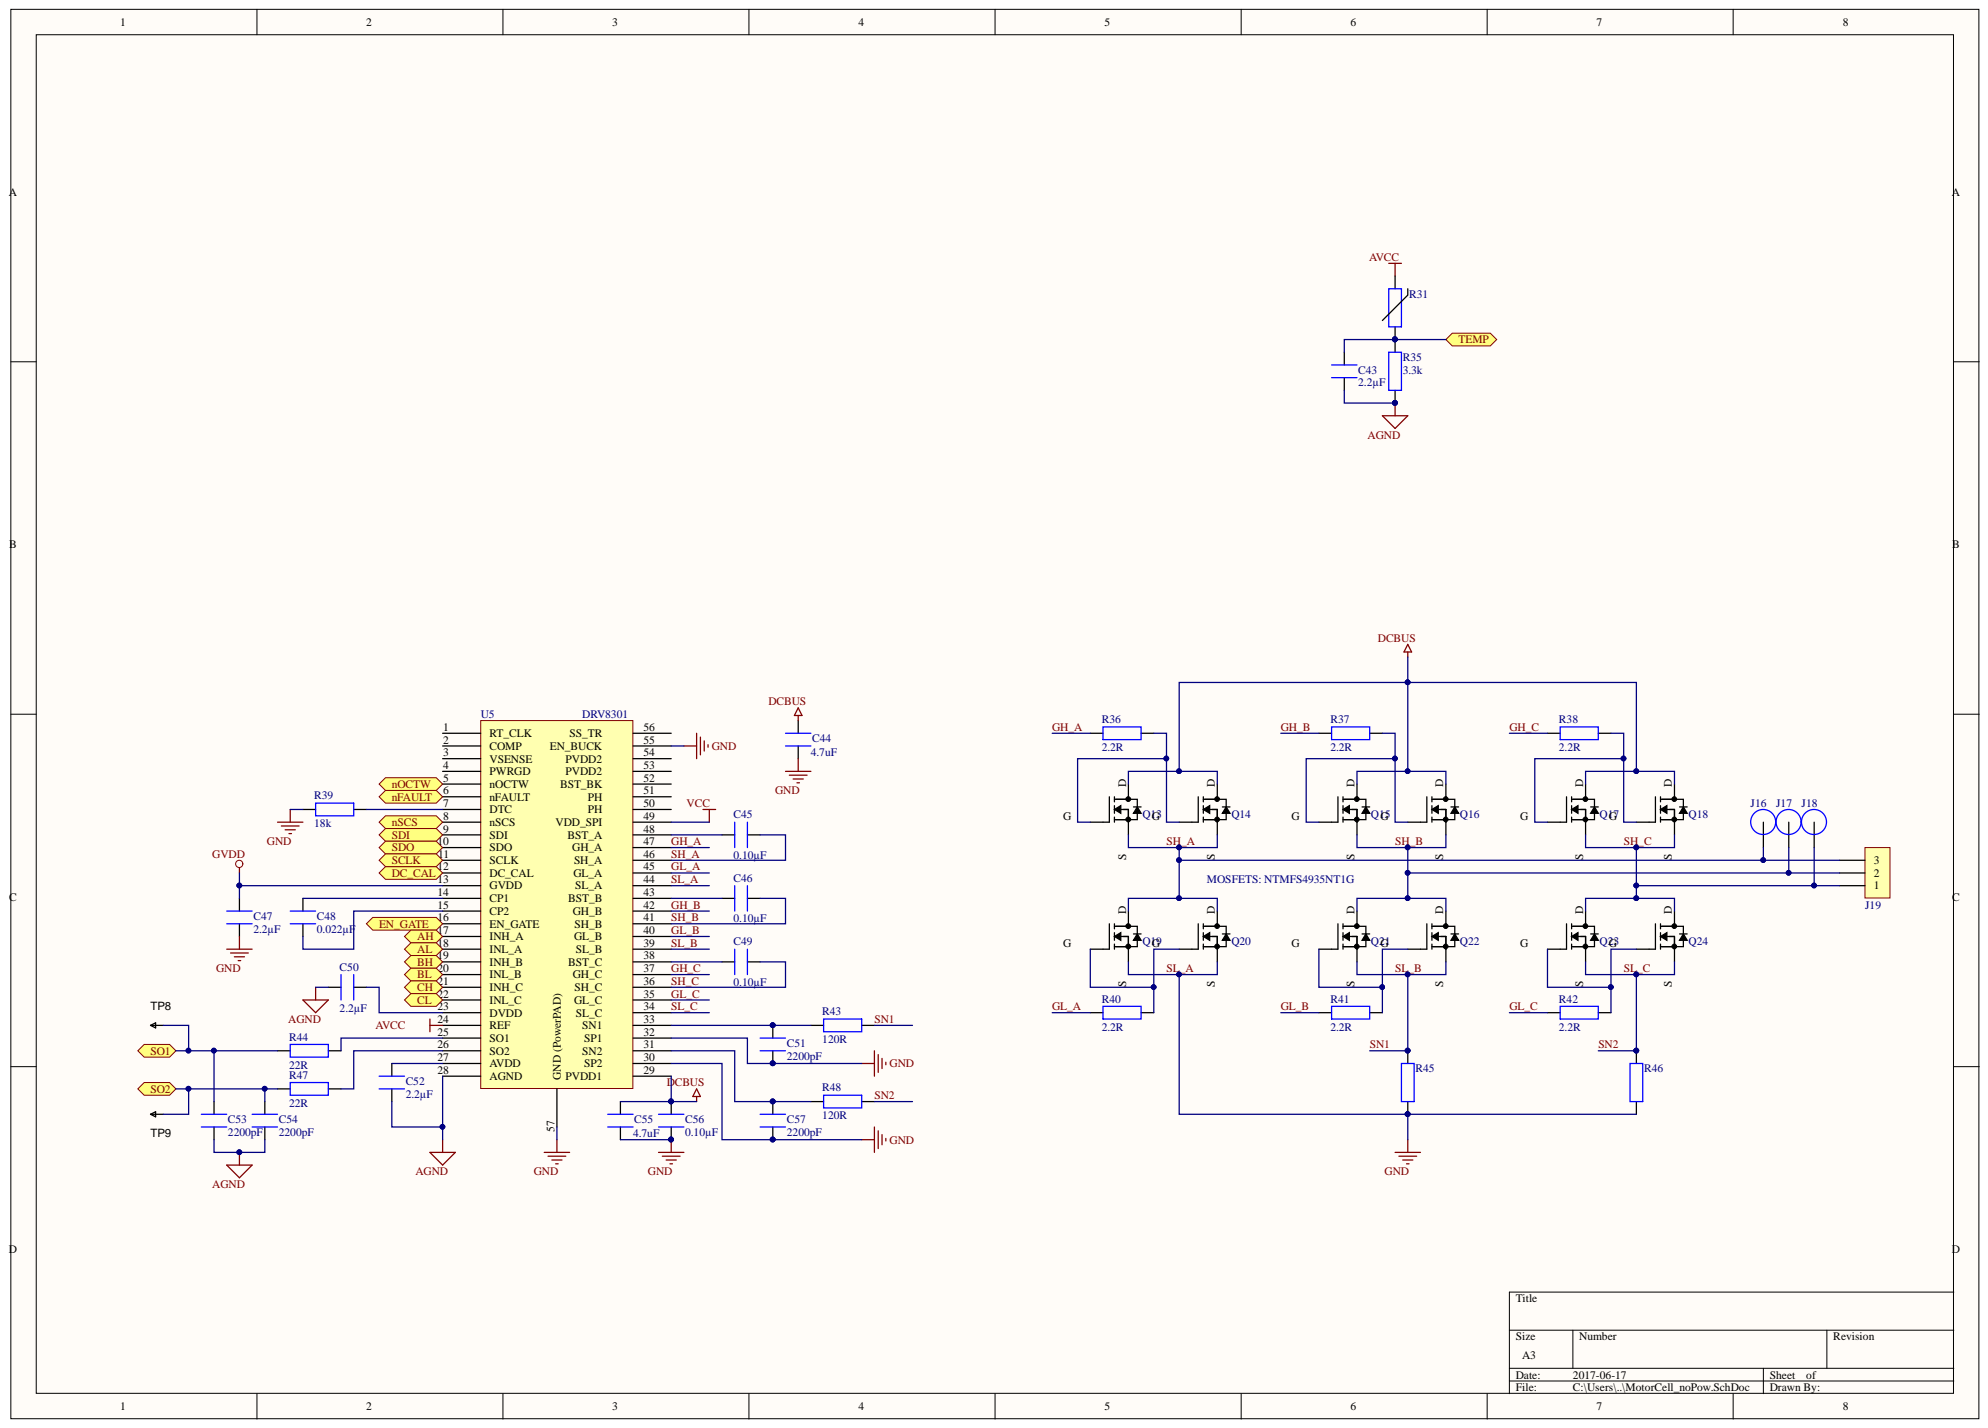
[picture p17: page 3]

C48 EN_GATE 0.022µF AH | | EN_GATE 16 | | SH_B

INH_A 17 | GL_B
INL_A 18 | SL_B

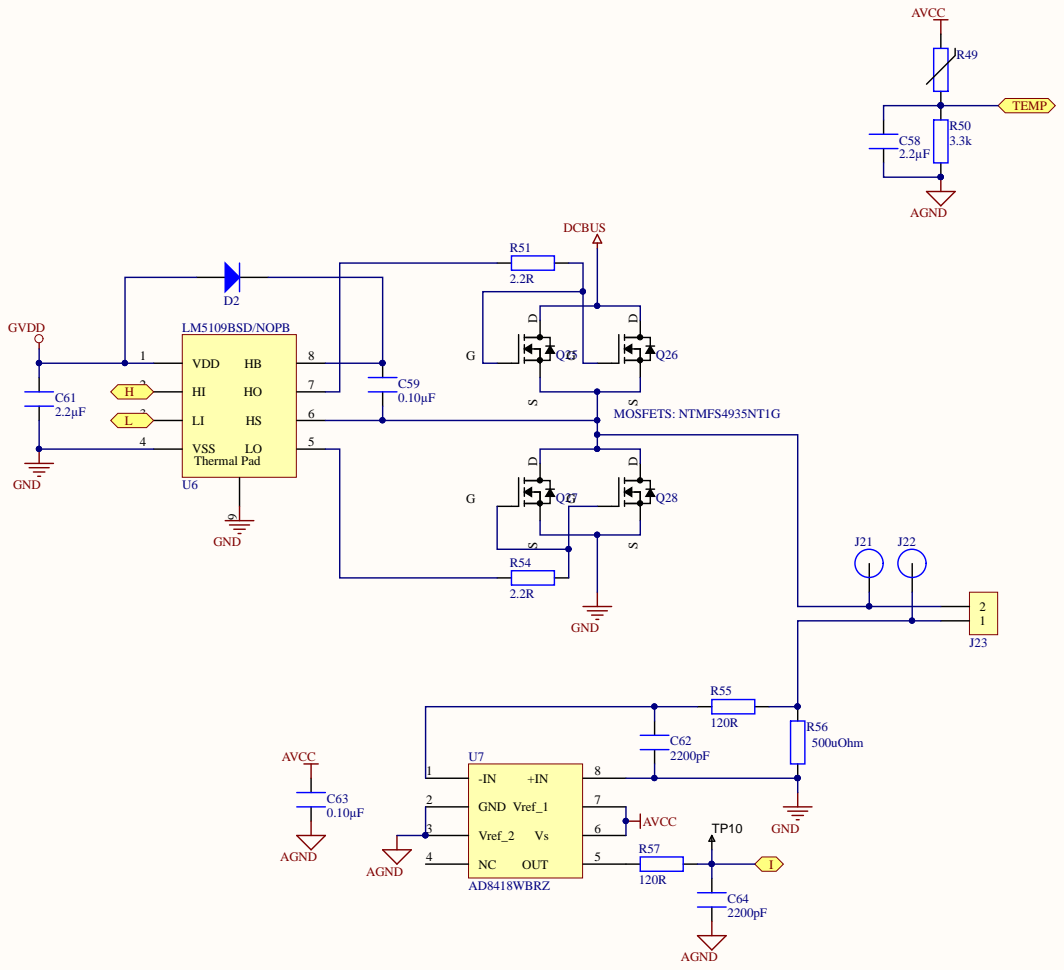
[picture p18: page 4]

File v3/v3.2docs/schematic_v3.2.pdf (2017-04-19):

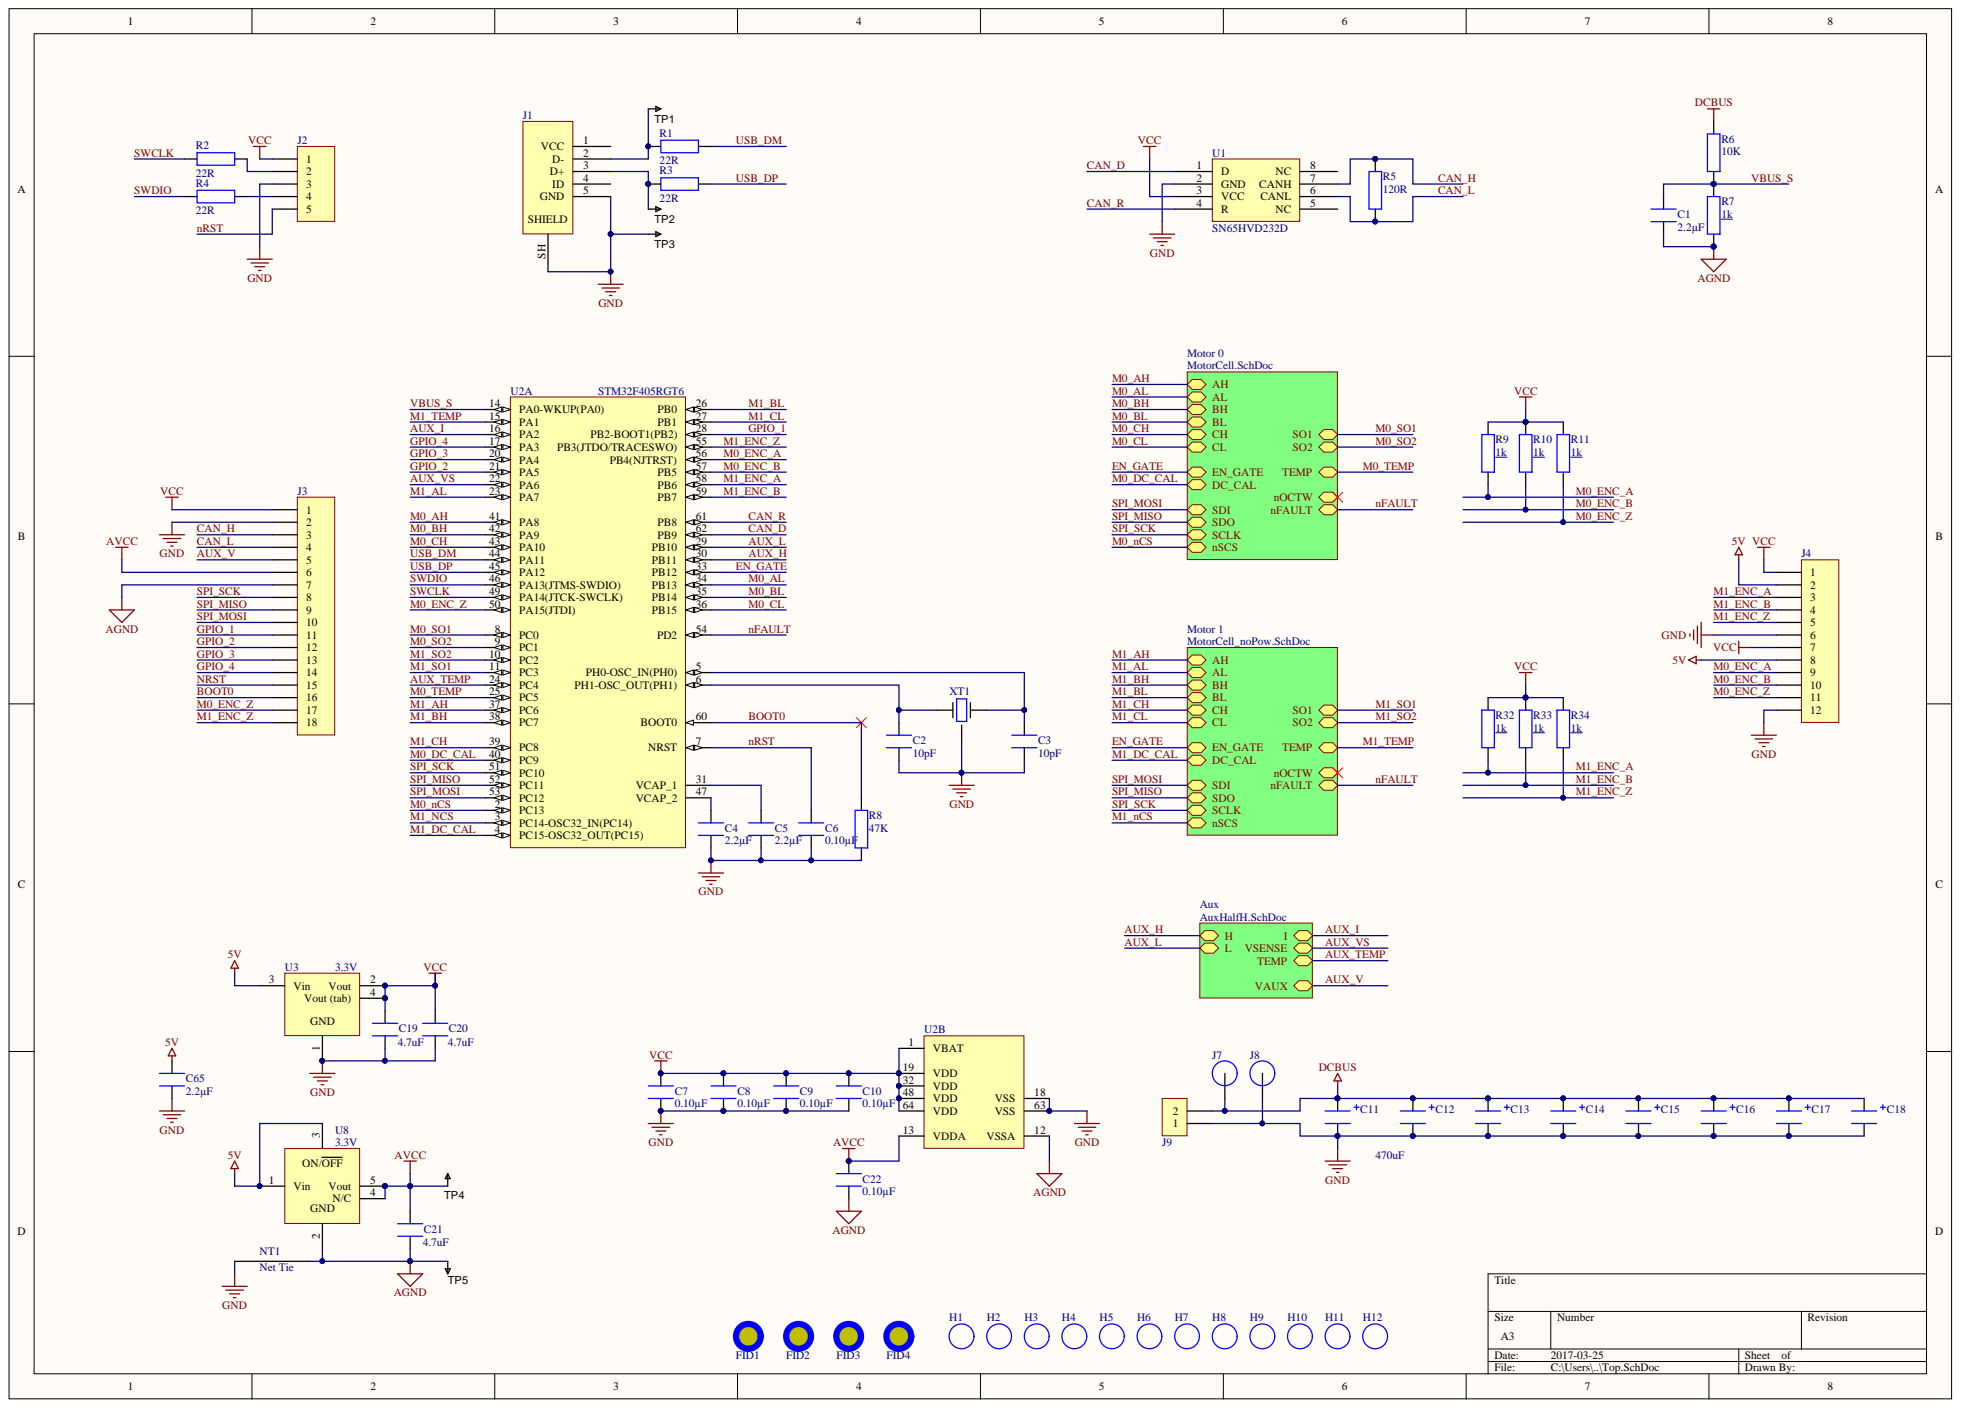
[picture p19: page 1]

1 2 3 4 5 6 7 8 9 10 11 12 13 14 15 16 17 18 | M0_AH | PA8 41 | CAN_R

CAN_H | | M0_BH | PA9 42 | CAN_D

SPI_SCK | SWCLK | PA14(JTCK-SWCLK) 49 | M0_BL M1_ENC_A
SPI_MISO | M0_ENC_Z | PA15(JTDI) 50 | M0_CL M1_ENC_B

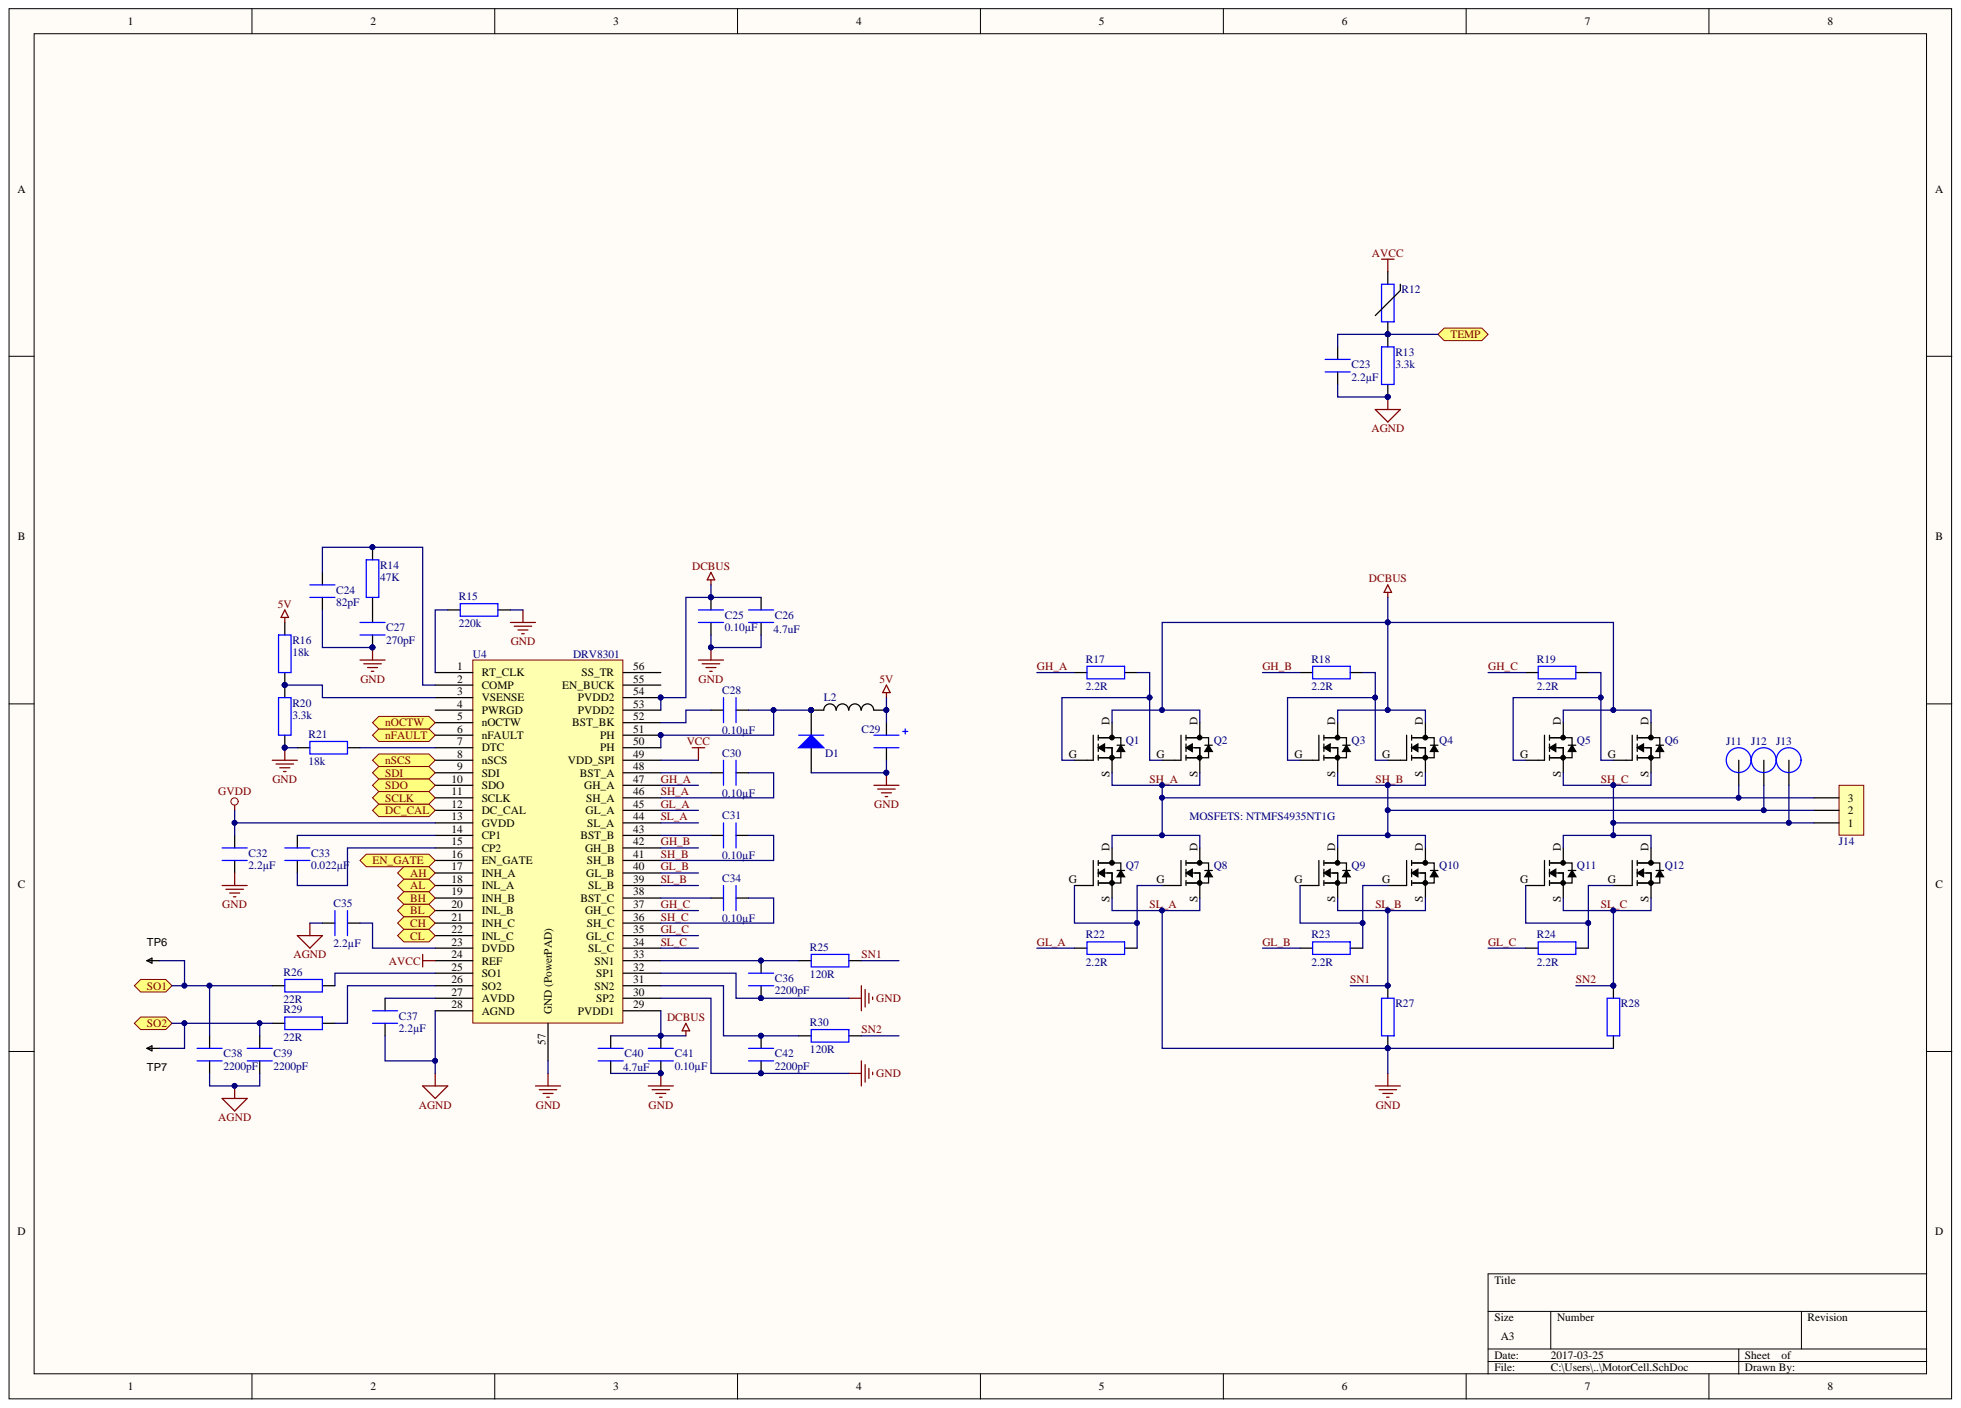
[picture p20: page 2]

C33 EN_GAT E 0.022 µ F AH | | | SH_B

INH_A 17 | GL_B
INL_A 18 | SL_B

DVDD 23 | SL_C

C37 | | DCBUS | R30
2.2 µ F

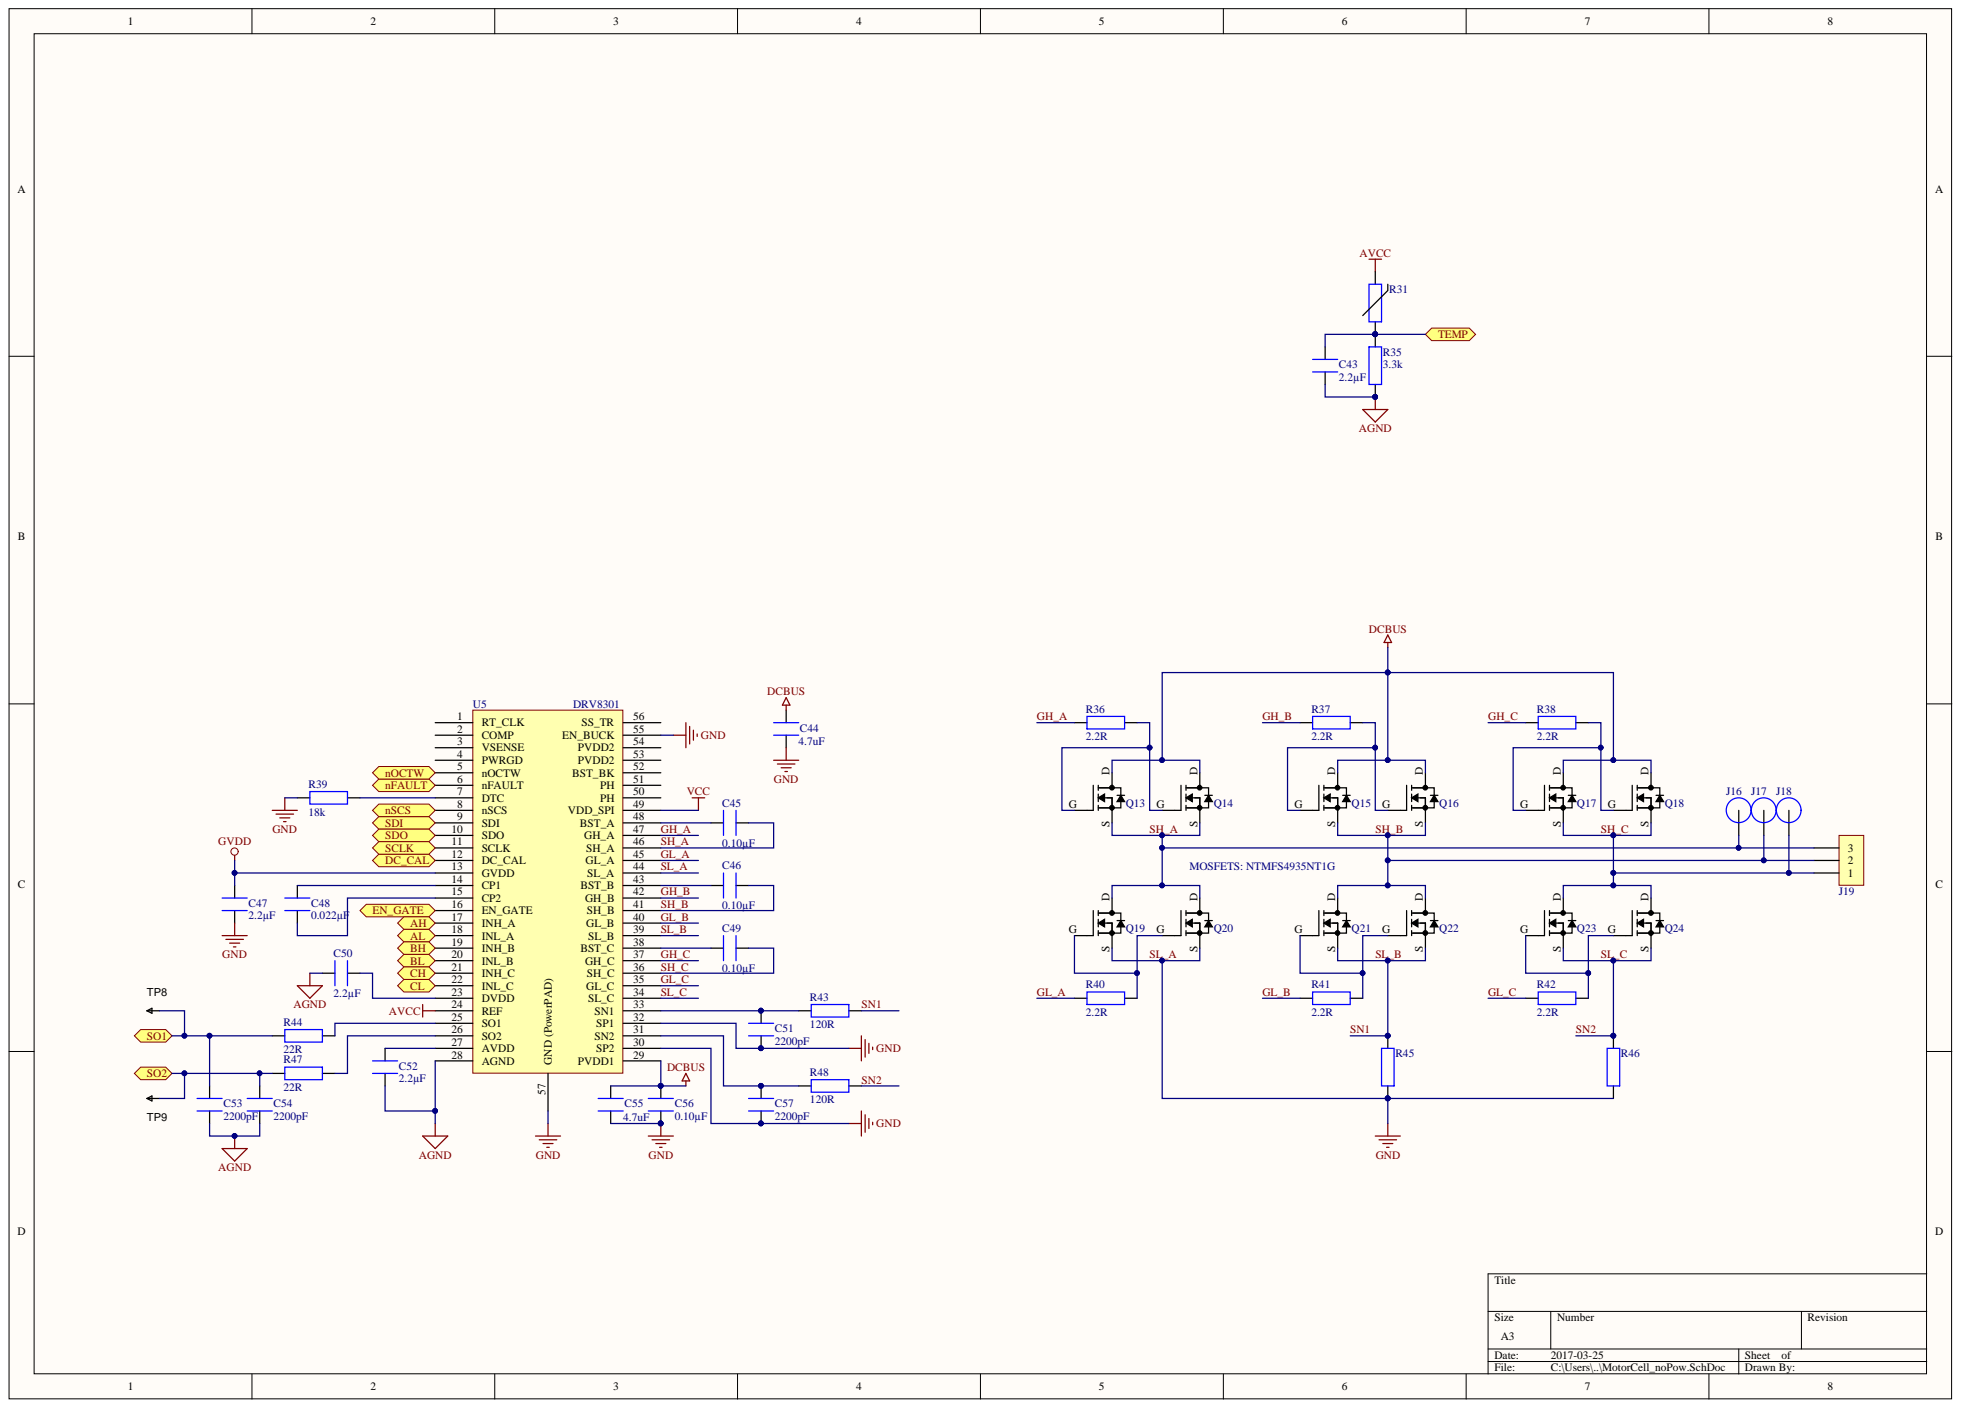
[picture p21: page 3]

GVDD 13 | SL_A
CP1 14
CP2 15 | | GH_B | 0.10µF

C48 EN_GATE 0.022µF AH | | EN_GATE 16 | | SH_B

INH_A 17 | GL_B
INL_A 18 | SL_B

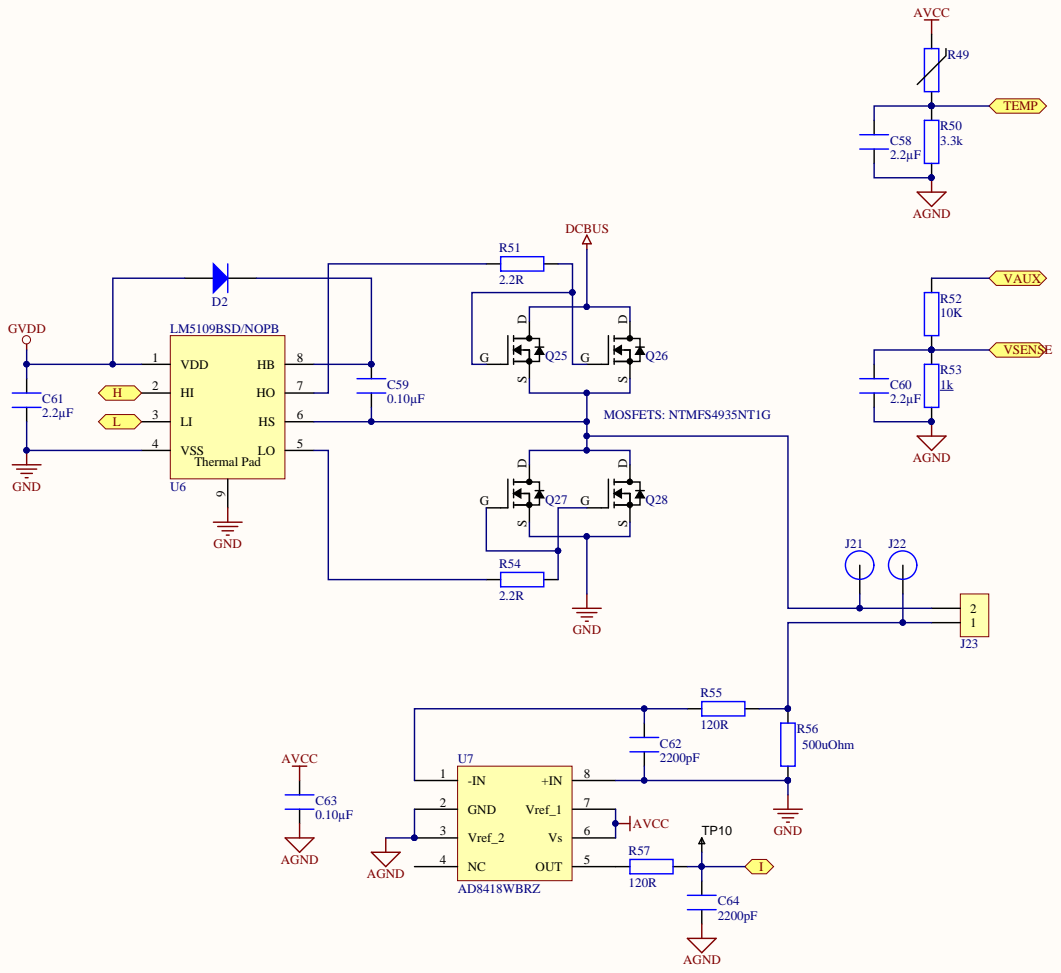
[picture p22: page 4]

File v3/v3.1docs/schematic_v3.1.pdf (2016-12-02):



R21 | PWRGD 4

nFAULT 6 | | VCC

CP1 14
CP2 15 | | GH_B | 0.10µF

C33 EN_GATE 0.022µF AH | EN_GATE 16 | | SH_B

INH_A 17 | GL_B
INL_A 18 | SL_B

C37 | | DCBUS | R30
2.2µF


C48 EN_GATE 0.022µF AH | | EN_GATE 16 | | SH_B

INH_A 17 | GL_B
INL_A 18 | SL_B

SO2 26 | | C51
AVDD 27 | | 0.022µF


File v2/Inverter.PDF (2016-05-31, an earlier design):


GND | | GND



IO_1A_7/ADC1IN2/DIFFIO_RX_L1P 7
IO_1A_8/ADC1IN3/DIFFIO_RX_L3N 8
IO_1A_10/ADC1IN4/DIFFIO_RX_L3P 10
IO_1A_11/ADC1IN5/DIFFIO_RX_L5N 11
IO_1A_12/ADC1IN6/DIFFIO_RX_L5P 12
IO_1A_13/ADC1IN7/DIFFIO_RX_L7N 13
IO_1A_14/ADC1IN8/DIFFIO_RX_L7P 14


Place close to FPG



Place with 5x5mm thermal pad
Thermal limit 500mA

GND__42 42
GND__53 53
GND__63 63
GND__68 68
GND__83 83
GND__95 95

GND__116 116
GND__125 125
GND__133 133
GND__137 137
GND__142 142

Thermal Pad 145




Comme nt | Descript | Designa tor | Footpri nt | LibRef | Quantit y | Value | Manufa cturer | Manufa cturer 1 Part | Supplier | Supplier Currenc y 1 | Supplier Order Qty 1 | Supplier Part | Supplier Stock 1 | Subtotal Supplier | Supp lier Price Unit

10M08S AE144 | | U6 | SQFP50 P2200X2 200X165 _HS-145N | 10M08S AE144 | | 1

ERJ3RQ FR33V | RESISTO R, 0603, 0.1W, 1%, 0R33 | R51 | RESC160 8X55N | ERJ3RQ FR33V | | 1 0.33 | PANASO NIC ELECTR ONIC COMPO NENTS | ERJ3RQ FR33V | Farnell | GBP | | 1 RL | 4895

FIDUCIA L | 1mm Fiducial with 2mm solderm ask, 3mm keepout | FID1, FID2, FID3, FID4, FID5, FID6, FID7 | FIDUCIA L | FIDUCIA L | | 7

FSM4JH | SWITCH, SPNO, 0.05A | SW1, SW2, SW3, SW4 | FSM4JH | FSM4JH | | 4 | TE CONNE CTIVITY / ALCOS WITCH | FSM4JH | Farnell | GBP | | 4 1555982 | 58711

Header 20X2 | Header, 20-Pin, Dual row | GPIO | HDR2X2 0 | Header 20X2 | | 1

Header 3 | Header, 3-Pin | ENC_VS EL | HDR1X3 | Header 3 | | 1

Header 4 | Header, 4-Pin | 3.3V, 5V, GND | HDR1X4 | Header 4 | | 3

Header 5 | Header, 5-Pin | 1J1, 2J1, 3J1 | HDR1X5 | Header 5 | | 3

M3 | M3 Hole with no copper | 1H1, 1H2, 2H1, 2H2, 3H1, 3H2 | M3 Hole | M3 Hole | | 6

M3 | M3 Mounti ng Hole | 1HS1, 1HS2, 2HS1, 2HS2, 3HS1, 3HS2 | M3 Mounti ng Hole | M3 Mounti ng Hole | | 6

M3 | M3 Spade Terminal | 1A, 1B, 1C, 2A, 2B, 2C, 3A, 3B, 3C, DC+, DC- | M3 Spade Hole | M3 Spade Terminal | | 11

M4 | M4 Mounti ng Hole | MH1, MH2, MH3 | MH_M4 | MH_M4 | | 3

MC0603 B104K16 0CT | CAP, MLCC, X7R, 100NF, 16V, 0603 | 1C10, 1C11, 2C10, 2C11, 3C10, 3C11, C17, C25, C26, C27, C28, C29, C30, C31, C32, C33, C43, C46, C47, C48, C49, C50, C54, C55, C56, C57, C58, C59, C65, C66 | 1608[06 03] | MC0603 B104K16 0CT | | 30 100nF | MULTIC OMP | MC0603 B104K16 0CT | Farnell | GBP | | 30 2310628 | 959995

MC0603 B471K50 0CT | CAP, MLCC, X7R, 470PF, 50V, 0603 | C42 | 1608[06 03] | MC0603 B471K50 0CT | | 1 470pF | MULTIC OMP | MC0603 B471K50 0CT | Farnell | GBP | | 1 1759079 RL | 23991

MC0603 N221J50 0CT | CAP, MLCC, C0G/NP 0, 220PF, 50V, 0603 | C13, C14, C15, C16, C18, C19, C20, C21 | 1608[06 03] | MC0603 N221J50 0CT | | 8 220pF | MULTIC OMP | MC0603 N221J50 0CT | Farnell | GBP | | 8 1759071 RL | 8340

MC0603 N470J50 0CT | CAP, MLCC, C0G/NP 0, 47PF, 50V, 0603 | C22, C23 | 1608[06 03] | MC0603 N470J50 0CT | | 2 47pF | MULTIC OMP | MC0603 N470J50 0CT | Farnell | GBP | | 2 1759062 | 42461

MC0603 X105K16 0 | CAP, MLCC, X5R, 1UF, 16V, 0603 | 1C4, 1C5, 1C6, 1C7, 1C8, 1C9, 2C4, 2C5, 2C6, 2C7, 2C8, 2C9, 3C4, 3C5, 3C6, 3C7, 3C8, 3C9, C12, C24, C34, C35, C36, C37, C38, C39, C40, C41, C44, C45, C63, C64 | 1608[06 03] | MC0603 X105K16 0 | | 32 1uF | MULTIC OMP | MC0603 X105K16 0CT | Farnell | GBP | | 32 2310630 | | -6

MC0805 F106Z10 0CT | CAP, MLCC, Y5V, 10UF, 0805 | C52, C53, C62 | CAPC20 12X135N | MC0805 F106Z10 0CT | | 3 10uF | MULTIC OMP | MC0805 F106Z10 0CT | Farnell | GBP | | 3 2408565 | 50995

MCMR0 6X1001F TL | RESISTO R, CERAMI C, 1K, 0.1W, 1% | R20, R24, R44, R45, R48, R49, R50, R53 | RESC160 8X55N | MCMR0 6X1001F TL | | 8 1k | MULTIC OMP | MCMR0 6X1001F TL | Farnell | GBP | | 8 2073348 | 460152

MCMR0 6X1002F TL | Resistor, 10k, 0603 | R18, R23, R25, R26, R27, R28, R29, R30, R31, R32, R33, R36, R37, R41, R42, R43, R46, R47, R54, R55 | RESC160 8X06L | MCMR0 6X1002F TL | | 20 10k | MULTIC OMP | MCMR0 6X1002F TL | Farnell | GBP | | 20 2073349 | 672642

MCMR0 6X3001F TL | RESISTO R, 0603, 3K, 1%, ANTI SULFUR | 1R1, 1R2, 1R3, 1R4, 1R5, 1R6, 2R1, 2R2, 2R3, 2R4, 2R5, 2R6, 3R1, 3R2, 3R3, 3R4, 3R5, 3R6, R19, R52 | RESC160 8X55N | MCMR0 6X3001F TL | | 20 3k | MULTIC OMP | MCMR0 6X3001F TL | Farnell | GBP | | 20 2073461 | 15083

MCSDR H125B-221MHF | INDUCT OR, 220µH, 20%, 2PINS | L1 | Inductor 12x12m m | MCSDR H125B-221MHF | | 1 200uH | MULTIC OMP | MCSDR H125B-221MHF | Farnell | GBP | | 1864461 1 RL | | 786

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



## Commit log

2016-05-31 Hardware repository split
    [10M08SAREVERSIONTEST_Library.SchLib, Analouge.SchDoc, AuxHalfH.SchDoc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]
2016-06-25 rename v3.0 bom saves
    [v3.0_BOM_nonsplit.xlsx, v3.0_BOM_split.xlsx]
2016-06-25 Done with first round of fixes for v3.1
    [AuxHalfH.SchDoc, CustomComponents.SchLib, CustomFootprints.PcbLib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]
2016-07-24 add schematic and bom
    [BOM_v3.1rc.xlsx]
2016-07-24 add test probe 1x and 5x
    [CustomComponents.SchLib, CustomFootprints.PcbLib, two_ax_PCB.PrjPcb]
2016-07-31 add USB testpoints
    [CustomComponents.SchLib, Top.SchDoc, two_ax_PCB.PrjPcb]
2016-12-02 schematic pdf and BOM updated to v3.1rc2 (add USB test points)
    [BOM_v3.0_nonsplit.xlsx, BOM_v3.0_split.xlsx, BOM_v3.1rc.csv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]
2017-01-13 Added More Documentation
    Added More Documumentation including a Produce_Documentation output job
    to make keeping the docs upto date much easier, and Assembly_BOM.PCBDwf.
    Documentaion.PDF is the output from Produce_Documentation
    [two_ax_PCB.PrjPcb]
2017-01-23 Corrected Silk Screen Mistake ( M0 M1 Designators on Encoder inputs swapped)
    [PCB.PcbDoc]
2017-01-24 Maybe altium and git dont work well together...
    [two_ax_PCB.PrjPcb]
2017-03-13 consolidate 0.1in headers
    [AuxHalfH.SchDoc, MotorCell.SchDoc, MotorCell_noPow.SchDoc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]
2017-03-22 Fix current filter values
    [AuxHalfH.SchDoc, CustomComponents.SchLib, MotorCell.SchDoc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]
2017-03-23 make analog testpoint breakout
    [AuxHalfH.SchDoc, MotorCell.SchDoc, MotorCell_noPow.SchDoc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]
2017-03-23 add precision LDO for AVCC
    [CustomComponents.SchLib, Top.SchDoc]
2017-03-25 add fiducials
    [Top.SchDoc]
2017-03-25 realign heatsink mounting holes
2017-03-25 change mosfets to more available version (NTMFS4935NT1G)
    [AuxHalfH.SchDoc, CustomComponents.SchLib, MotorCell.SchDoc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]
2017-03-25 add v3.2 docs
    [AuxHalfH.SchDoc, BOM_v3.0_nonsplit.xlsx, BOM_v3.0_split.xlsx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]
2017-03-26 remove unknown files
    [two_ax_PCB.PrjPcb]
2017-06-02 Add v3.2 STEP file
    [PCB.step]
2017-06-08 flip cap and vreg, add secondary DC pads
    [two_ax_PCB.PrjPcb]
2017-06-08 add power LED
    [CustomComponents.SchLib, PCB.PcbDoc, Top.SchDoc]
2017-06-10 change terminal blocks to 7.62mm pitch
    [AuxHalfH.SchDoc, CustomComponents.SchLib, CustomFootprints.PcbLib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]
2017-06-10 remap GPIO pins, discard auxV
    [AuxHalfH.SchDoc, PCB.PcbDoc, Top.SchDoc]
2017-06-17 increase encoder pullups to 3k3 for better compatibility with push-pull encoders
    [PCB.PcbDoc, Top.SchDoc]
2017-06-17 added v3.3 docs
    [BOM_v3.3.csv, BOM_v3.3_bottom.csv, BOM_v3.3_top.csv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]
2017-09-04 add mechanical dimensions
    [PCB.PcbDoc]
2017-09-04 dimensions in mm
    [PCB.PcbDoc]
2017-11-04 fix ground issue, shunt via resistance
    [AuxHalfH.SchDoc, CustomComponents.SchLib, CustomFootprints.PcbLib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]
2017-11-07 Add 48V variation
    [AuxHalfH.SchDoc, CustomComponents.SchLib, MotorCell.SchDoc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]
2017-11-07 add 48V silkscreen
    [PCB.PcbDoc]
2018-01-26 add second shunt net-ties
    [MotorCell.SchDoc, MotorCell_noPow.SchDoc, PCB.PcbDoc]
2018-01-26 Move GVDD caps from PGND to GND
    [MotorCell.SchDoc, MotorCell_noPow.SchDoc, PCB.PcbDoc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]
2018-06-09 add v3.4 docs
    [BOM_v3.4_24V.csv, BOM_v3.4_48V.csv, PCB_v3.4.step]
2018-07-23 add v3.5 docs
    [PCB_v3.5.step]
